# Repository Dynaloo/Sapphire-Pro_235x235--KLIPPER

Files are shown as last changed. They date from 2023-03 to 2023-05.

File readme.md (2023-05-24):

# Configuring Printer - Sapphire-Pro 235x235 (core XY)

- SKR 1.4 turbo with
- 4x TMC2209 UART
- 24v power MEAN WELL — LRS-350
- BLtouch V3.1 ANTCLABS
- Neopixel (12 leds)
- V6 Hotend - plated copper heat block & nozzel - titanium alloy heat break 
- 2x T8 screew - Pitch 2mm Lead 2mm

- Rock PI4 (substitute the Rasberry PI4 which is currently not found)

- KLIPPER (https://www.klipper3d.org/)
- Fluiddpi (https://docs.fluidd.xyz/)

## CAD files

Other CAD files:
CAD/Z Guidage Assembly.dwg
CAD/Z Bed Assembly_v3.dwg
CAD/Z T8 Assembly.dwg
CAD/Gantry Assembly.dwg
CAD/Z Motor.dwg
CAD/IDLE_MOTOR_RIGHT.dwg
CAD/IDLE_FRONT_LEFT.dwg
CAD/IDLE_MOTOR_LEFT.dwg
CAD/IDLE_FRONT_RIGHT.dwg

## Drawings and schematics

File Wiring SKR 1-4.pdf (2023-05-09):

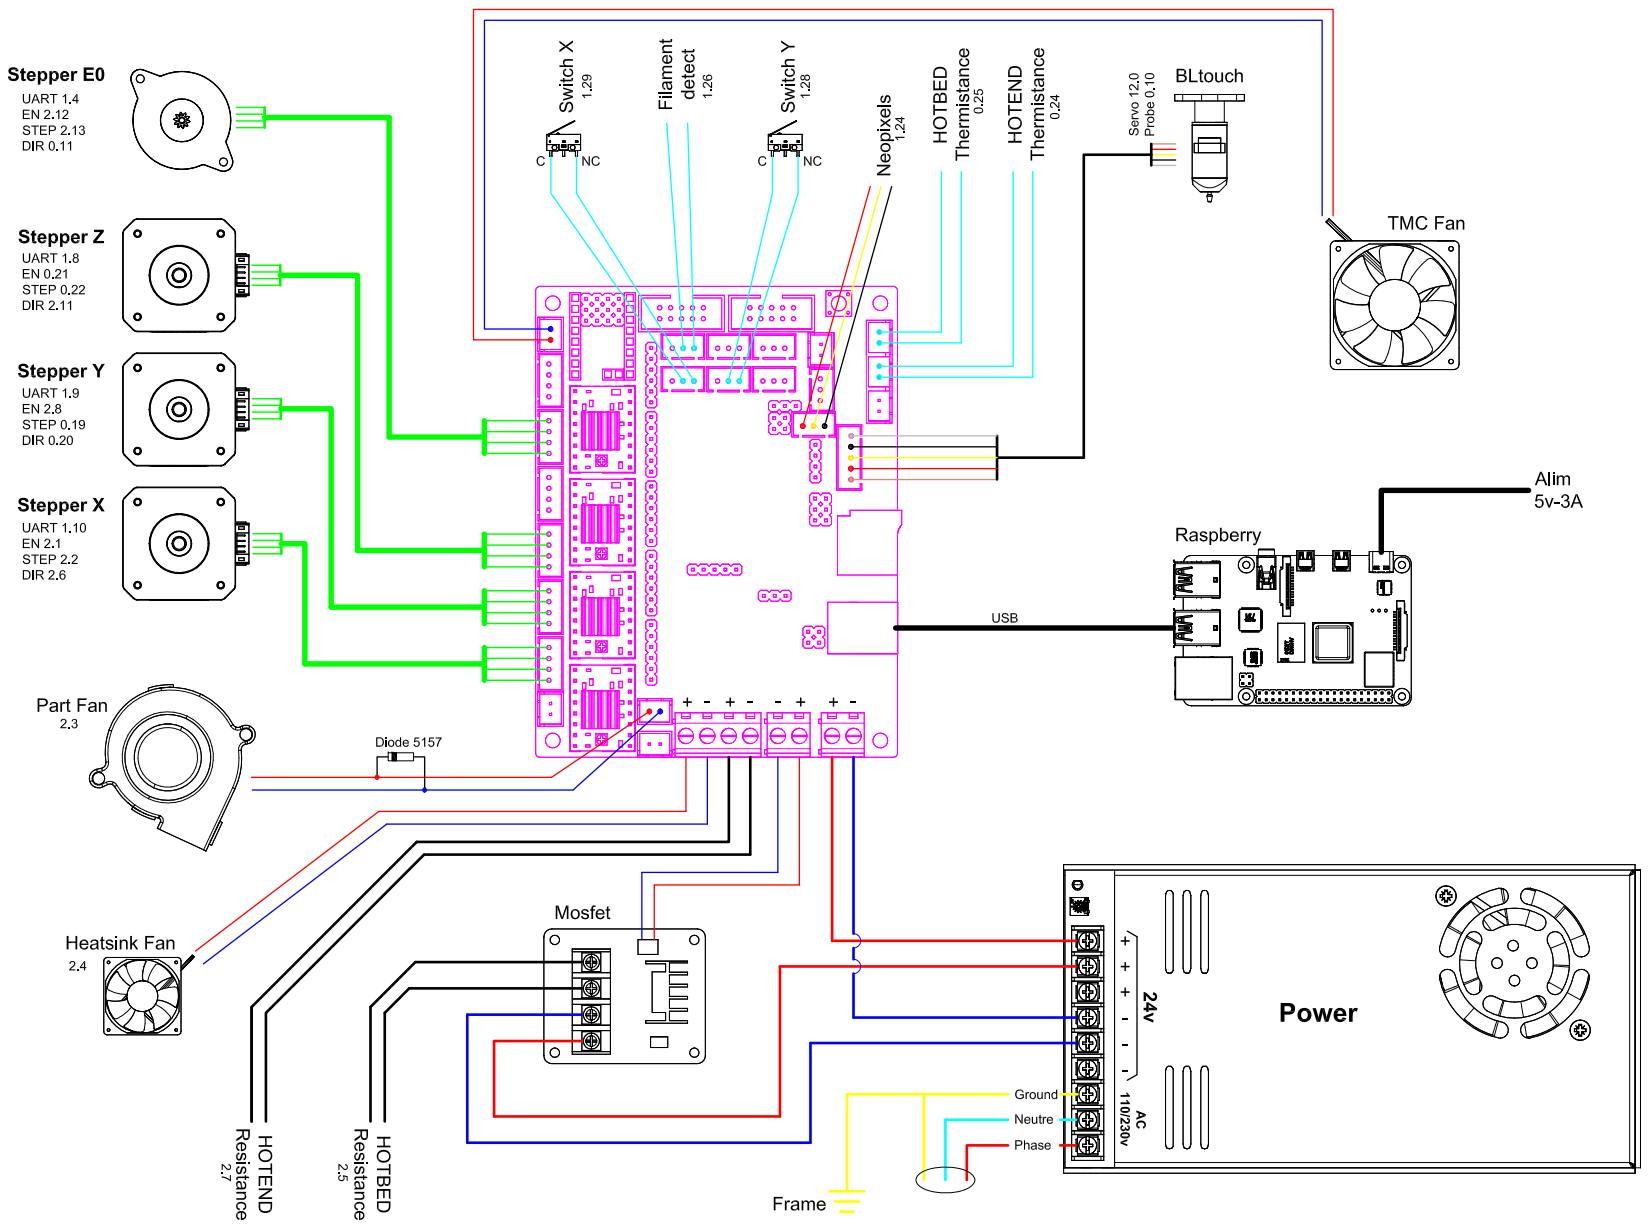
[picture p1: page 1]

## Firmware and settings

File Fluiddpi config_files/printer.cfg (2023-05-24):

# This file contains common pin mappings for the BIGTREETECH SKR V1.4 board (LPC1768 or LPC1769).

# X Y Z E - TMC2209 UART

# X - Motor Usongshine US-17HS4401S
# Y - Motor Usongshine US-17HS4401S
# Z - Motor Usongshine US-17HS4401S
# E - Motor LDO-36STH20-1004AHG

# Sherpa mini Extruder 

# See "https://www.klipper3d.org/Config_Reference.html" for a description of parameters.

# Pin names preceded by ! indicate that a reverse polarity should be used.
# Pins name preceded by ^ to indicate that a hardware pull-up resistor should be enabled for the pin.


########################################
# Parametre MCU
########################################
##SSH command  "ls /dev/serial/by-id/*"

[mcu]
serial: /dev/serial/by-id/usb-Klipper_lpc1769_0BE0000AA49869AF34F13E5EC62000F5-if00


########################################
# Fichier de configuration
########################################

[include ./fluidd.cfg]

[include ./probe.cfg] #add for BlTouch probe

[respond] #add for adaptative bed mesh

[include ./macros.cfg]

[include ./macro_bed_mesh.cfg] #add for adaptative bed mesh

[include ./macro_neopixel.cfg] #add for neopixels

[include ./macro_loop_test.cfg] #add for speed velocity & acceleration test


########################################
# Parametres Imprimante
########################################

[stepper_x]
step_pin: P2.2
dir_pin: !P2.6
enable_pin: !P2.1
microsteps: 16
rotation_distance: 40
endstop_pin: ^P1.29 # For safety, microswitch wiring on NC with Pull up
position_endstop: 0
position_max: 230
homing_speed: 30

[stepper_y]
step_pin: !P0.19
dir_pin: !P0.20
enable_pin: !P2.8
microsteps: 16
rotation_distance: 40
endstop_pin: ^P1.28 # For safety, microswitch wiring on NC with Pull up
position_endstop: 0
position_max: 230
homing_speed: 30

[stepper_z]
step_pin: P0.22
dir_pin: P2.11
enable_pin: !P0.21
microsteps: 16
rotation_distance: 2
#homing_positive_dir: false
endstop_pin: probe:z_virtual_endstop #!P1.27
#position_endstop: 0.5
position_min: -10
position_max: 200

[extruder]
step_pin: P2.13
dir_pin: !P0.11
enable_pin: !P2.12
microsteps: 16
rotation_distance: 23.1
gear_ratio: 50:10
nozzle_diameter: 0.400
filament_diameter: 1.750
max_extrude_only_distance: 150.0
pressure_advance: 0.08
pressure_advance_smooth_time: 0.030
heater_pin: P2.7
sensor_type: EPCOS 100K B57560G104F
sensor_pin: P0.24
control: pid
pid_kp: 18.168
pid_ki: 0.797
pid_kd: 103.560
min_temp: 0
max_temp: 260
min_extrude_temp: 190

#[extruder1]
#step_pin: P1.15
#dir_pin: P1.14
#enable_pin: !P1.16
#heater_pin: P2.4
#sensor_pin: P0.23
#...

[heater_bed]
heater_pin: P2.5
sensor_type: EPCOS 100K B57560G104F
sensor_pin: P0.25
control: pid
pid_kp: 72.789
pid_ki: 1.116
pid_kd: 1187.376
min_temp: 0
max_temp: 110
#pwm_cycle_time: 0.02 # 50hz for european AC 230v, to avoid flickering lights.


########################################
# FAN
########################################

[fan]
## Print cooling fan
pin: P2.3

[heater_fan Heatsink_fan]
## Heatsink cooling Fan
pin: P2.4
max_power: 1
fan_speed: 1
kick_start_time: 0.5
hardware_pwm: false
heater: extruder
heater_temp: 40.0
shutdown_speed: 0


########################################
# PRINTER
########################################

[printer]
kinematics: corexy
max_velocity: 250
max_accel: 5000
max_z_velocity: 15
max_z_accel: 500
max_accel_to_decel: 5000
square_corner_velocity: 10.0

[gcode_arcs]
resolution: 0.2

[firmware_retraction]
retract_length: 0.8
retract_speed: 40
unretract_extra_length: 0
unretract_speed: 60


########################################
# TMC2209 drivers configuration
########################################

[tmc2209 stepper_x]
uart_pin: P1.10
run_current: 0.800
#interpolate: False
#hold_current: 0.600
sense_resistor: 0.110
stealthchop_threshold: 0

[tmc2209 stepper_y]
uart_pin: P1.9
run_current: 0.800
#interpolate: False
#hold_current: 0.600
sense_resistor: 0.110
stealthchop_threshold: 0

[tmc2209 stepper_z]
uart_pin: P1.8
run_current: 0.800
interpolate: False
#hold_current: 0.600
sense_resistor: 0.110
stealthchop_threshold: 0

[tmc2209 extruder]
uart_pin: P1.4
run_current: 0.6
interpolate: False
#hold_current: 0.600
sense_resistor: 0.110
stealthchop_threshold: 0

#[tmc2209 extruder1]
#uart_pin: P1.1
#run_current: 0.800
#interpolate: False
#hold_current: 0.600
#sense_resistor: 0.110
#stealthchop_threshold: 0


########################################
# Board LCD pins
########################################

[board_pins]
aliases:
    # EXP1 header
    EXP1_1=P1.30, EXP1_3=P1.18, EXP1_5=P1.20, EXP1_7=P1.22, EXP1_9=<GND>,
    EXP1_2=P0.28, EXP1_4=P1.19, EXP1_6=P1.21, EXP1_8=P1.23, EXP1_10=<5V>,
    # EXP2 header
    EXP2_1=P0.17, EXP2_3=P3.26, EXP2_5=P3.25, EXP2_7=P1.31, EXP2_9=<GND>,
    EXP2_2=P0.15, EXP2_4=P0.16, EXP2_6=P0.18, EXP2_8=<RST>, EXP2_10=<NC>
    # Pins EXP2_1, EXP2_6, EXP2_2 are also MISO, MOSI, SCK of bus "ssp0"

# RepRapDiscount Full Graphic Smart Controller
[display]
lcd_type: st7920
cs_pin: EXP1_4
sclk_pin: EXP1_5
sid_pin: EXP1_3
encoder_pins: ^EXP2_3, ^EXP2_5
click_pin: ^!EXP1_2
#kill_pin: ^!EXP2_8

[output_pin beeper]
pin: EXP1_1


########################################
# NEOPIXELS
########################################

[neopixel NeoPixels]
pin: P1.24
#   The pin connected to the neopixel. This parameter must be
#   provided.
chain_count: 12
#   The number of Neopixel chips that are "daisy chained" to the
#   provided pin. The default is 1 (which indicates only a single
#   Neopixel is connected to the pin).
color_order: GRB
#   Set the pixel order required by the LED hardware. Options are GRB,
#   RGB, GRBW, or RGBW. The default is GRB.
initial_RED: 0.0
initial_GREEN: 0.0
initial_BLUE: 0.0
#initial_WHITE: 0.0
#   Sets the initial LED color of the Neopixel. Each value should be
#   between 0.0 and 1.0. The WHITE option is only available on RGBW
#   LEDs. The default for each color is 0.


########################################
# ROCK PI4
########################################

[temperature_sensor rock_pi4]
sensor_type: temperature_host
min_temp: 10
max_temp: 100


########################################
# Filament switch sensor
########################################

[filament_switch_sensor my_sensor]
pause_on_runout: True
runout_gcode: pause
insert_gcode: resume
event_delay: 3.0
pause_delay: 0.5
switch_pin: P1.26


########################################
# Resonance Compensation
########################################

[input_shaper]
shaper_freq_x: 77.8
shaper_type: mzv
shaper_freq_y: 60.4
shaper_type: mzv

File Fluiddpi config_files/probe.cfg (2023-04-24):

[bltouch]
sensor_pin: ^P0.10
control_pin: P2.0
samples: 2
sample_retract_dist: 5.0
probe_with_touch_mode: True
x_offset: -32.9
y_offset: -5
z_offset: 2.915
stow_on_each_sample: True
# Some BLTouch V3 and many clones apparently require this, though mine didnt:
#pin_up_reports_not_triggered: True
#pin_up_touch_mode_reports_triggered: True
#flavor: genuine_smart_3.1
pin_move_time: 1

[safe_z_home]
home_xy_position: 142, 124 # Change coordinates to the center of your print bed
speed: 50
z_hop: 10 # Move up 10mm
z_hop_speed: 5

[bed_mesh]
speed: 100
horizontal_move_z: 8
mesh_min: 10, 25
mesh_max: 195, 210
probe_count: 7, 7
algorithm: bicubic
#fade_start: 1
fade_end: 10
#fade_target: 0
relative_reference_index: 24 #add for adaptative bed mesh



#*# <---------------------- SAVE_CONFIG ---------------------->
#*# DO NOT EDIT THIS BLOCK OR BELOW. The contents are auto-generated.
#*#
#*# [bltouch]
#*# z_offset = 1.258

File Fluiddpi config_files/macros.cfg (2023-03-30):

#  __  __                          
# |  \/  |                         
# | \  / | __ _  ___ _ __ ___  ___ 
# | |\/| |/ _` |/ __| '__/ _ \/ __|
# | |  | | (_| | (__| | | (_) \__ \
# |_|  |_|\__,_|\___|_|  \___/|___/
#
# Configuration macro

# In SuperSlicer, as start gcode
  # START_PRINT BED_TEMP={material_bed_temperature_layer_0} EXTRUDER_TEMP={material_print_temperature_layer_0} SIZE={first_layer_print_min[0]}_{first_layer_print_min[1]}_{first_layer_print_max[0]}_{first_layer_print_max[1]}

# In SuperSlicer, as finish gcode
  # END_PRINT

######################################################################
# Macros Start Print and End Print
######################################################################

[gcode_macro START_PRINT]
description: Macro start print
gcode:
   G21 # metric values
   G90 # absolute positioning
   M107 # start with fan off

     #Get Bed & Extruder temperature from Slicer GCode
      {% set BED_TEMP = params.BED_TEMP|default(50)|float %}
      {% set EXTRUDER_TEMP = params.EXTRUDER_TEMP|default(190)|float %}
      {% set FL_SIZE = params.SIZE|default("0_0_0_0")|string %} #add for adaptative bed mesh

   M140 S{BED_TEMP} # start heating bed
   #M190 S{BED_TEMP} # wait until bed headed

   M109 S160 # wait for nozzle temperature to 160°C

   G28 # Home XYZ
   ADAPTIVE_BED_MESH SIZE={FL_SIZE} #add for adaptative bed mesh
   #BED_MESH_PROFILE load=mesh_bed

   G1 X5.0 Y5.0 Z20.0 F5000 ; Move to start position & Z +20mm
   
   M190 S{BED_TEMP} # Heat bed
   M109 S{EXTRUDER_TEMP} T0 # Heat nozzle

   PURGE # Load gcode macro PURGE

[gcode_macro PURGE]
description: Macro purge
gcode: 
    M82 # set extruder to absolute mode
    G92 E0 # set position extruder
    G1 E10 F200 # extrude 10mm of feed stock

    G92 E0 # set position extruder
    G1 Z5.0 F3000 # Move Z Axis up little to prevent scratching of Heat Bed

    G1 X3.0 Y20 Z0.3 F5000 # Move to start position
    G1 X3.0 Y100 Z0.3 F1500 E7 # Draw the first line
    G1 X3.3 Y100 Z0.3 F5000 # Move to side a little
    G1 X3.3 Y20 Z0.3 F1500 E14 # Draw the second line
    
    G92 E0 # Set position Extruder
    G1 E-1 F500 # Retract filament by 1 mm
    G1 Z2.0 F3000 # Move Z Axis up little to prevent scratching of Heat Bed
    G1 X10 Y20 Z0.3 F300 # Move over to prevent blob squish
    M220 S100 # set feedrate 100%
    G92 E0 # Set position Extruder

[gcode_macro END_PRINT]
description: Macro end print
gcode:
    G91 # Relative positioning
    G1 E-5 F300 # retract the filament a bit before lifting the nozzle, to release some of the pressure
    G1 Z5 F5000 # move Z up a bit

    G90 # Absolute positioning
    G1 X5 Y200 F5000 # To move the printhead away

    M104 S0 # Turn off heater nozzel
    M140 S0 # Turn off heater bed
    M106 S0 # Turn Fan off
    M84 # disable steppers
    BED_MESH_CLEAR


######################################################################
# Macros "BED MESH LEVELING"
######################################################################

[gcode_macro BED_LEVELING]
description: Nivellement du plateau
gcode:
  {% if printer.idle_timeout.state == "Printing" %}
  RESPOND TYPE=error MSG="Impossible de lancer cette macro actuellement !"
  {% else %}
  {% if printer.toolhead.homed_axes != "xyz" %}
  G28
  {% endif %}
  G1 X0 Y0 Z50 F2500
  BED_MESH_CALIBRATE
  G1 X5 Y5 Z10 F2500
  BED_MESH_PROFILE save=mesh_bed
  #G28
  {% endif %}

#[gcode_macro G29] #old version
#description: Nivellement du plateau
#gcode:
#    G28
#    BED_MESH_CALIBRATE
#    G0 X5 Y5 Z10 F5000
 #   BED_MESH_PROFILE save=mesh_bed


######################################################################
# Macros "BED SCREWS ADJUST"
######################################################################

[gcode_macro Bed_screws_adjust]
description: Reglage plateau avec les vis
gcode:
    G28
    SCREWS_TILT_CALCULATE  


######################################################################
# Macros "Z Adjust"
######################################################################

[gcode_macro Z_OFFSET_CALIBRATION]
description: Calibrer le Z-Offset
gcode:
  G28
  G1 X0 Y0 Z50 F2500
  #M400
  PROBE_CALIBRATE

[gcode_macro ZUP]
gcode:
    SET_GCODE_OFFSET Z_ADJUST=0.01 MOVE=1
	
[gcode_macro ZDOWN]
gcode:
    SET_GCODE_OFFSET Z_ADJUST=-0.01 MOVE=1


######################################################################
# Macro Calibration du PID Buse / Plateau
######################################################################

[gcode_macro CALIBRATION_PID_BED]
description: PID Plateau
gcode:
  {% if printer.idle_timeout.state == "Printing" %}
  RESPOND TYPE=error MSG="Impossible de lancer cette macro actuellement !"
  {% else %}
  G28
  M106
  G1 Z50 F1500
  PID_CALIBRATE HEATER=heater_bed TARGET={params.TEMP|default(65)}
  G28
  SAVE_CONFIG
  {% endif %}
  
[gcode_macro CALIBRATION_PID_HOTEND]
description: PID Hotend
gcode:
  {% if printer.idle_timeout.state == "Printing" %}
  RESPOND TYPE=error MSG="Impossible de lancer cette macro actuellement !"
  {% else %}
  G28
  M106
  G1 Z50 F1500
  PID_CALIBRATE HEATER=extruder TARGET={params.TEMP|default(200)}
  G28
  SAVE_CONFIG
  {% endif %}


##################################################
# Sauvegarde des paramètres
##################################################

[gcode_macro SAUVEGARDER]
description: Sauvegarder la configuration
gcode:
  SAVE_CONFIG


##################################################
# Chargement / Retrait du filament
##################################################

[gcode_macro UNLOAD_FILAMENT]
description: Retrait du filament
gcode:
  {% if printer.idle_timeout.state == "Printing" and not printer.pause_resume.is_paused %}
  RESPOND TYPE=error MSG="Impossible de lancer cette macro actuellement !"
  {% else %}
  SAVE_GCODE_STATE NAME=unload_state
  {% if printer.extruder.temperature < 200 %}
  RESPOND MSG="Chauffe..."
  M109 S200
  {% endif %}
  RESPOND MSG="Retrait du filament..."
  G91
  G1 E2 F400
  G1 E-80 F800
  RESTORE_GCODE_STATE NAME=unload_state
  {% endif %}


[gcode_macro LOAD_FILAMENT]
description: Chargement du filament
gcode:
  {% if printer.idle_timeout.state == "Printing" and not printer.pause_resume.is_paused %}
  RESPOND TYPE=error MSG="Impossible de lancer cette macro actuellement !"
  {% else %}
  SAVE_GCODE_STATE NAME=load_state
  {% if printer.extruder.temperature < 200 %}
  RESPOND MSG="Chauffe..."
  M109 S200
  {% endif %}
  RESPOND MSG="Chargement du filament..."
  G91
  G1 E80 F300
  M400
  RESTORE_GCODE_STATE NAME=load_state
  {% endif %}


##################################################
# Screws tilt ajust
##################################################

  #[bed_screws]
#screw1: 6,3
#screw2: 216,3
#screw3: 216,214
#screw4: 6,214

[screws_tilt_adjust]
screw1: 59, 39
screw1_name: ecrou avant gauche
screw2: 228, 39
screw2_name: ecrou avant droite
screw3: 228, 210
screw3_name: ecrou arriere droite
screw4: 59, 210
screw4_name: ecrou arriere gauche
horizontal_move_z: 10
speed: 50
screw_thread: CW-M4


######################################################################
# Macros Tuning "PRESSURE ADVANCE"
######################################################################

[gcode_macro PA_tunning]
description: Tuning Pressure Advance direct drive
gcode: 
	SET_VELOCITY_LIMIT SQUARE_CORNER_VELOCITY=1 ACCEL=500
	TUNING_TOWER COMMAND=SET_PRESSURE_ADVANCE PARAMETER=ADVANCE START=0 FACTOR=.005

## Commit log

2023-03-28 Stepper extruder modified
    motor LDO-36STH20-1004AHG
    [printer.cfg]
2023-03-28 Length load/unload filament modified
    [macros.cfg]
2023-03-30 Add command MCU
    [printer.cfg]
2023-04-15 Update endstop_pin X and Y
    # For safety, X-Y microswitch wiring on NC with pull up
    [printer.cfg]
2023-05-24 Add files via upload
    Update
    [printer.cfg]
